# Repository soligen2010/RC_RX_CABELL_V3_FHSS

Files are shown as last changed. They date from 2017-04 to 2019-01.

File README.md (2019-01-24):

# RC_RX_CABELL_V3_FHSS
## Background
RC_RX_CABELL_V3_FHSS is an open source receiver for remote controlled vehicles.  Developed by Dennis Cabell (KE8FZX)
The hardware for this receiver is an Arduino Pro Mini (using a 5V ATMEGA328P at 16 Mhz) and one or two NRF24L01+ modules.  Both are inexpensively available on-line.  Be sure to get the version of a Pro Mini that has pins A4, A5, A6 and A7 broken out.

The transmitter side of this RC protocol is in the Multi-protocol TX Module project at [https://github.com/pascallanger/DIY-Multiprotocol-TX-Module]( https://github.com/pascallanger/DIY-Multiprotocol-TX-Module).

Since there are on-going changes to the main Multi-protocol branch, if you have issues or are using experimental features please test with the solgen2010 fork, which is the latest version tested with the receiver [https://github.com/soligen2010/DIY-Multiprotocol-TX-Module]( https://github.com/soligen2010/DIY-Multiprotocol-TX-Module).

Note: The no-pulses failsafe feature has not yet been merged into pascallanger. Use the soligen2010 fork if you want to use this feature.

## The Protocol
The protocol used is named CABELL_V3 (the third version, but the first version publicly released).  It is a FHSS protocol using the NRF24L01+ 2.4 GHz transceiver.  45 channels are used from 2.403 through 2.447 GHz.  The reason for using 45 channels is to keep operation within the overlap area between the 2.4 GHz ISM band (governed in the USA by FCC part 15) and the HAM portion of the band (governed in the USA by FCC part 97).  This allows part 15 compliant use of the protocol, while allowing licensed amateur radio operators to operate under the less restrictive part 97 rules if desired.

Each transmitter is assigned a random ID (this is handled by the Multi-protocol TX Module) based on this ID one of 362880 possible channel sequences is used for the frequency hopping.  The hopping pattern algorithm ensures that each hop moves at least 9 channels from the previous channel.  One packet is sent every 3 - 4 milliseconds (depending on options chosen), changing channels with each packet. All 45 channels are used equally.

The CABELL_V3 protocol can be configured to send between 4 and 16 RC channels, however this receiver software is currently only capable of outputting up to 8 channels via PWN or PPM.  This is because only 8 channels were conveniently laid out on the Arduino Pro Mini, and more than 8 channels over PPM would be too slow.  SBUS output allows all 16 channels to be used.

I recommend reducing the number of channels as much as possible based on what your model requires.  Fewer channels will use a smaller packet size, which improves transmission reliability (fewer bytes sent means less opportunity for errors).

The protocol also assigns each model a different number so one model setting does not control the wrong model.  The protocol can distinguish up to 255 different models, but be aware that the Multi-Protocol transmitter software only does 16.

## Hardware
A 5V 16Mhz Arduino Pro Mini and one or 2 NRF24L01+ modules are needed for this receiver.  Be sure to get the version of a Pro Mini that has pins A4 and A5 broken out (and A6, A7 too for telemetry analog inputs).  The [hardware folder](https://github.com/soligen2010/RC_RX_CABELL_V3_FHSS/tree/master/hardware) contains a schematic and a PCB layout using a single transceiver module for PWN or PPM output; however, this version of the PCB has not been tested.  I am still using the previous version of the PCB and modifying it to implement the changes included in the new version. If anyone tries this PCB version, please open an issue let me know how it works. 

There is also a schematic for using 2 NRF24L01 modules for diversity.  If anyone designs a board for this, please contribute it.  This schematic also has the signal inverter needed for SBUS.

The PA+LNA versions of the NRF24L01+ module provide more receiver range and reliability than the non PA+LNA versions, However the less expensive modules also work OK if the on-board antenna is replaced with a better antenna, although randomly some units seem to work well and others not so well.  I recommend range testing each module.  These modules are also typically unshielded, but work better when shielded.  Here is an outline of the modifications (TODO: add pictures)

#### Antenna
* For the PA_LNA module that has an SMA Connector, remove the connector. A small butane torch to heat the connector works well.  When the solder melts, it pulls right off 
* Cut the antenna trace.  On the PA+LNA module cut the trace back far enough so that no portion of the trace extends beyond the ground plane on the back of the board.  For the boards with an antenna, cut the trace leading to the antenna shortly after the last surface mount component (a capacitor, I think).
* Scrape or sand away the solder mask over the antenna trace.  On the boards with an antenna you will also need to sand away the area next to the trace for a ground connection.  For the PA+LNA module you can re-use the ground connections that were used for the connector.
* Tin the ground and antenna attachment points with solder
* Strip back the coax and separate the braid, twisting it into a wire that can be soldered to the ground point. Tin this.
* Strip the center conductor back to within 1mm of where the braided part now ends.  Tin this.
* Solder the coax to the board.  Use hot glue to fix the coax to the board as strain relief.
* On the other end of the coax, strip back and remove the braided ground conductor to leave the center wire exposed to form the antenna. Leave the inner wire insulation on.

I am no expert, but based on the best understand I have been able to achieve on the theory, using RG-178 or RG-316 (both have speed factor of 69.5) the calculated theoretical coax lengths to use are:
* For the shielded portion of the coax, ideally make the length a multiple of 42.5 mm.  170mm seems like a good length. 
* The length of the antenna at the end should theoretically be 32.5mm (based on center frequency of 2.425 GHz.  I don’t have the proper equipment to verify these lengths, experiment for what works best for you.  My tests showed 32mm seems to work better than 32.5 for a monopole antenna.

The antennas that come with the PA/LNA modules on EBay are often not very good.  Get a good antenna for your transmitter.  For the transmitter I use a 5dbi antenna constructed as recommend by Andrew McNeil at [https://www.youtube.com/watch?v=bs8hvXGJdhM](https://www.youtube.com/watch?v=bs8hvXGJdhM).  Good RX and TX antennas make a big difference to performance.

#### Shielding
Shielding will require using 2 layers of heat shrink tubing around the whole module.  

* First solder a bare wire onto a ground point on the board.
* Encase as much of the board as possible in heat shrink tubing, leaving the antenna and ground wire sticking out, and don’t cover the pins.
* Use copper tape to wrap the module as much as possible on the heat shrink tubing, while staying away from the edge of the heat shrink. (Aluminum  tape can work too, but you cant solder to it.)
* Bend the ground wire back over the copper tape and solder it to the copper tape.
* Encase as much of the board as possible again in heat shrink tubing.  Don’t cover the pins. Be sure to cover all the ground wire and copper tape shielding.

These shielding steps are based partially  in the article at [http://blog.blackoise.de/2016/02/fixing-your-cheap-nrf24l01-palna-module/](http://blog.blackoise.de/2016/02/fixing-your-cheap-nrf24l01-palna-module/). Using the heat shrink and soldering the copper tape is a more robust implementation of the same concept.

## Receiver Output
The output method is controlled via the option byte in the protocol header.  See the Taranis Setup section for  more details.
* Sum PPM on Arduino pin D2 (the Roll pin). The channel sequence is AETR, more specifically Roll, Pitch, Throttle, Yaw, AUX1, AUX2, AUX3, AUX4.
* Individual PWM channel output on pins D2 through D9 in the sequence Roll, Pitch, Throttle, Yaw, AUX1, AUX2, AUX3, AUX4.
* SBUS (__Experimental__) output on the TX pin through an inverter.  The channel sequence is AETR, more specifically Roll, Pitch, Throttle, Yaw, AUX1, AUX2, AUX3, AUX4, AUX5, AUX6, AUX7, AUX8, AUX9, AUX10, AUX11, AUX12.  SBUS packets are output every 7 milliseconds.

## Receiver Setup
The receiver must be bound to the transmitter. There are several ways for the receiver to enter Bind Mode.  When a receiver is in bind mode the LED will be on.
* A new Arduino will start in bind mode automatically.  Only an Arduino that was flashed for the first time (not previously bound) does this.  Re-flashing the software will retain the old binding unless the EEPROM has been erased.
* Erasing the EEPROM on the Arduino will make it start up in bind mode just like a new Arduino. The Arduino sketch [here]( https://github.com/soligen2010/Reset_EEPROM) will erase the EEPROM.
* Connect the Bind Jumper, or press the Bind button while the receiver powers on.
* The protocol has a Un-bind command (it erases the EEPROM), after which a re-start will cause the receiver to enter bind mode just like a new Arduino. After an Unbind the LED will blink until the receiver is re-started.

Turn on the transmitter and have it send a Bind packet.  The receiver LED changes from always on to a slow blink when the bind is successful.  Re-start the receiver after the bind and take the transmitter out of Bind mode, then test the connection.

## Fail-safe
The receiver fail-safes after 1 second when no packets are received.  If a connection is not restored within 3 seconds then the receiver will disarm.  
* At fail-safe, the throttle is set to minimum, and the other channels are set to the failsafe value.
* After disarm, the throttle will stay at minimum until the receiver is re-armed.  To re-arm the receiver move the throttle to the minimum position.
* If FailsafeNu Pulses is used, then all output signals cease on failsafe (Both PPM and SBUS signals are discontinued)

When a receiver is bound the failsafe values are reset to the default values, which are throttle minimum and all other channels at mid-point.

### Customizing Fail-safe Values
__Do not set fail-safe values while in flight.__  Due to the length of time it takes to write the new fail-safe values to EEPROM, the receiver may go into fail-safe mode while saving the values, causing loss of control of the model.  Before flying a model, always test the fail-safe values after they have been set.

Fail-safe set mode will set the fail-safe values.  This can be done one of two ways:
* A set-Fail-Safe packet can be sent from the transmitter.  The values from the first packet in a series for set-Fail-Safe packets are saved as the new fail-safe values.  The LED is turned on when a set-Fail-Safe packet is received, and stays on as long as set-Fail-Safe packets continue to be received.  The LED is turned off when set-Fail-Safe values stop being received
* After the receiver has initialized, the bind button (or bind jumper) can be held for one to 2 seconds until the LED is turned on.  The values from the first packet received after the LED is turned on will be saved as the new fail-safe values.  The LED will turn off when the button is released (or jumper removed).

When fail-safe set mode is entered, the LED is turned on and stays on until the failsafe set mode is exited.  Only the values from the first packet received in fail-safe set mode are saved (this is to avoid accidentally using up all of the EEPROMs limited number of write operations)

Values for all channels can be set except for the throttle channel.  The fail-safe for throttle is always the minimum throttle.

If the receiver was bound with Failsafe No Pulses, then customizing values does not apply.

## Safety

__Always remove the props when working on a model!__

The receiver has a dis-arm feature to help prevent the motor from unintentionally spinning, however no system is 100%, so take care whenever you power up a model.  __Keep all body parts, clothing, and other objects out of the path of the prop.__

Many ESCs and flight controllers have an arm sequence where the throttle must be set to minimum or some other condition to be met in order to arm.  This receiver also has the following arm/disarm behavior which complements ESC and flight controller arming behavior.

When powered on the __receiver starts out in an armed state__. However, if no signal is detected within 3 seconds the receiver dis-arms.  The receiver also dis-arms if an RC signal is lost for 3 seconds. While dis-armed, only the minimum value will be sent on the throttle channel.  The receiver will re-arm when it receives an RC signal with a minimum value for the throttle channel.  If your model disarms in while in use, move the throttle to its minimum position to re-arm once the RC signal has been re-established.

Powering on the model before the transmitter will cause the receiver to dis-arm in 3 seconds as long as there is no RC signal.  During this power on time there is no output from the receiver until an RC signal is first received from the transmitter, so the ESC or flight controller will not arm if it requires a signal to arm.

Powering the transmitter off before the model will cause the receiver to dis-arm after 3 seconds, forcing the throttle channel to minimum.

There is a 10k pull-up resistor on pin D2 that is essential for safety when using PPM.  This resistor prevents random signals from being output from the receiver while it is initializing.  

### Sending Stick Commands to ESC

__Stay Safe!  Only do this with props removed!__

The reason the receiver initializes in an armed state to to allow an ESC to be configured with stick commands, which may require the initial throttle setting sent to the ESC to be max throttle. If you power on the transmitter before the model, then when the model acquires the signal the values received will be immediately output.  This means that a high throttle will be immediately output.  __Do not do this if your ESC starts in an armed state!__

Please refer to your ESC documentation for details on configuring it with stick commands.

## Diversity
Diversity is achieved by using 2 NRF24L01 modules, which improves link reliability. Try to orient the antennas close to 90 degrees to each other so at least one antenna has a good orientation to the transmitter antenna.  The use of a second NRF24L01 module for diversity is optional.  The code automatically detects if one or 2 modules are connected.  See the "with diversity" schematic in the hardware folder for how to wire the NRF24L01 modules.

Both modules listen for an incoming packet.  If the primary receiver does not get a packet when expected, the secondary receiver is checked for the missed packet.  After each packet, the primary/secondary receivers are swapped, except in the case where only the primary receiver had the packet, in which case this receiver will retain the primary role.  Telemetry packets are transmitted using the same receiver that was used to read the packet.  If both receivers got the incoming packet, then the packet in the secondary receiver is discarded.  The net effect is that the receivers alternate with each packet, except when only one receiver is receiving, in which case that receiver continues to be used for both the primary receiver and telemetry transmit.

## Taranis Setup using Multi-Protocol Module and Open-TX 2.2

With a Multi Protocol module installed in the Taranis, this is how to configure a model to use this protocol.  These instructions for for a Serial connection using OpenTX 2.2.  These instructions assume some familiarity with using OpenTX on the Taranis.

### Initial Setup 
   
* Press Menu to go to Model Selection and Select the model you with to set up.
* Press Page to get the the Model Setup page.
* Scroll down to the Internal RF section and change Mode to OFF.
* Scroll down to the External RF section and change Mode to MULT.
* In the protocol field to the right of MULT, select Custom.
* In the protocol field to the right of Custom, enter 34.  This is the protocol number. 
  * __This number is temporary.  It likely will need to change when the TX half of this protocol is merged into the main Multi-Protocol project.__
* The next number to the right is the sub-protocol.  For initial setup select 0 or 1.  Valid values are:
  * 0 - Normal usage without telemetry
  * 1 - Normal usage with telemetry (please see the section on telemetry)
  * 6 - Set fail-safe values (see below and the Fail-safe section)
  * 7 - Unbind receiver (see below)
* Receiver No. should be filled in with the model number.
* Move down to the Option value.  This value must be calculated to configure the protocol.  This is done by entering a number that is the sum of the options you wish to use.  Select the values from below and add them together to get the option value.
  * _Channel Reduction_ reduces the number of channels transmitted.  This also reduces the size of the packet, which improves reliability. (Fewer bytes sent equates to less opportunity for error.)  For best reliability reduce the number of channels to the minimum number needed for the model. Note that at least 4 channels must always be sent.  Choose one of the following to add into the Option value:
    * 0  - Send 16 channels
    * 1  - Send 15 channels
    * 2  - Send 14 channels
    * 3  - Send 13 channels
    * 4  - Send 12 channels
    * 5  - Send 11 channels
    * 6  - Send 10 channels
    * 7  - Send 9 channels
    * 8  - Send 8 channels
    * 9  - Send 7 channels
    * 10 - Send 6 channels
    * 11 - Send 5 channels
    * 12 - Send 4 channels
  * _Output Mode_ indicates how the receiver should output the channels.  Choose one of the following to add into the Option value:
    * 0  - Output servo PWM signals on pins D2 through D9 for channels 1 to 8
	* 16 - Output channels 1 to 8 using PPM on pin D2
	* 32 - Output channels 1 to 16 using SBUS __(Experimental)__
  * _Transmitter Power_ Overrides the Multi-Protocol's normal high power setting.  See comments on power setting below.  Choose one of the following to add into the Option value:
    * 0 - Use the NRF24L01+ HIGH power setting.  This is the normal Multi-Protocol module behavior.
    * 64 - Use the NRF24L01+ MAX power setting instead of the HIGH power setting.  This over-rides the normal Multi-Protocol module behavior.
  #### Notes on Power Setting
  Using an NRF24L01+ with PA/LNA outputs 25 milliwatts for HIGH power and 100 milliwatts for MAX power.  Despite this there are reports that using MAX power on inexpensive Chinese modules provides worse range than using the HIGH power setting due to the noise added by the extra amplification and the lower quality Chinese components.  By adding shielding and using a good antenna, I get better range using MAX power even with Chinese components.  Your results may vary so range test your equipment and use the setting that provides the best results.

### Binding Receiver
* Turn on the receiver in Bind Mode. (See receiver setup above.)
* In the transmitter Navigate to the Model Setup page.
* In the External RF section, highlight BIND and press enter.
* The receiver LED will blink when the bind is successful.
* Restart the receiver.
 
### Unbinding Receiver

In order to un-bind a receiver using the transmitter, a model bound to the receiver must be configured in the transmitter.  With a model selected that is bound to the receiver:
* Navigate to the Model Setup page.
* Go to the External RF section.
* Change the sub-protocol (second number after "Custom") to 7.
* The receiver LED will fast blink when the un-bind is successful.
When the receiver is restarted, it will start in Bind mode.

### Setting Failsafe Values

__Do not set fail-safe values while in flight.__ Please see the Customizing Fail-safe Values section for more information.

* Navigate to the Model Setup page.
* Go to the External RF section.
* Place all switches in the desired fail-safe state.
* Move the sticks to the desired fail-safe state.  Hold them in this position until the fail-safe settings are recorded by the receiver.
* While holding the sticks, change the sub-protocol (second number after "Custom") to 6.  DO not go past 6.  If you even briefly go to 7 the receiver will un-bind.
* When the LED is turned on, the Fail-safe settings are recorded
* Change the sub-protocol back to its original setting. The LED will turn off.

Always test the Fail-safe settings before flying.  Turning off the transmitter should initiate a Fail-safe after one second.

### Setting Failsafe No Pulses (Experimental)

Failsafe No Pulses can only be set at bind time.  All servos will receive no pulses during a fail-safe, so custom fail safe values do not apply.  If the receiver is on SBUS output mode, the SBUS output is stopped during failsafe.

* Unbind the receiver.
* Navigate to the Model Setup page.
* Go to the External RF section.
* Change the sub-protocol to 5.  
* Perform the Bind procedure.
* Change the sub-protocol to the desired setting for flying.

If your output goes to a flight controller via SBUS, and the flight controller honors the SBUS failsafe flag (which is typical), then you probably do not want to use No Pulses because the SBUS protocol handles the failsafe appropriately.

Always test the Fail-safe settings before flying.  Turning off the transmitter should initiate a Fail-safe after one second.

## Telemetry

When the sub-protocol is set to Normal with Telemetry, the receiver sends telemetry packets back to the transmitter.  Three values are returned, a simulated RSSI, and the voltages on the Arduino pins A6 and A7.  A receiver module with diversity is recommended when using telemetry to increase the reliability of the telemetry packets being received by the transmitter.

### RSSI

Because the NRF24L01 does not have an RSSI feature, the RSSI value is simulated based on the packet rate.  The base of the RSSI calculation is the packet success rate from 0 to 100.  This value is re-calculated approximately every 1/2 second (every 152 expected packets).  This success percentage is then modified in real time based on packets being missed, so that if multiple packets in a row are missed the RSSI value drops without having to wait for the next re-calculation of the packet rate.

In practice, the packet rate seems to stay high for a long range, then drop off quickly as the receiver moves out of range.  Typically, the telemetry lost warning happens before the RSSI low warning.

The RSSI class encapsulates the RSSI calculations. If you are so inclined, feel free play with the calculation. If anyone finds an algorithm that works better, please contribute it. 

### Analog Values

Analog values are read on Arduino pins A6 and A7.  Running on a, Arduino with VCC of 5V, only values up to 5V can be read.  __A value on A6 or A7 that exceeds the Arduino VCC will cause  damage__, so care must be taken to ensure the voltage is in a safe range.

Values from pins A6 and A7 come into a Taranis transmitter as telemetry values A1 and A2.  You can use either of these to read battery voltage or the output of current sensor.  The following article explains how to input battery voltage to A2 on an Frsky receiver using a voltage divider.  The same method can be used to read battery voltage on this receiver.  [http://olex.biz/tips/lipo-voltage-monitoring-with-frsky-d-receivers-without-sensors](http://olex.biz/tips/lipo-voltage-monitoring-with-frsky-d-receivers-without-sensors).

The values sent are 0 - 255 corresponding to 0V - 5V.  This will need to be re-scaled to the actual voltage (or current, etc.) in the transmitter on the telemetry  configuration screen.

## Flashing Firmware

The Arduino development environment is required to compile the code and write the firmware to the Arduino Pro Mini. If you are not familiar with this, here are some resources to help you.

* [https://www.arduino.cc/en/Guide/HomePage](https://www.arduino.cc/en/Guide/HomePage)
* [https://www.arduino.cc/en/Guide/ArduinoProMini](https://www.arduino.cc/en/Guide/ArduinoProMini)
* [https://www.youtube.com/watch?v=78HCgaYsA70](https://www.youtube.com/watch?v=78HCgaYsA70)
* [http://lab.dejaworks.com/programming-arduino-mini-pro-with-ftdi-usb-to-ttl-serial-converter/](http://lab.dejaworks.com/programming-arduino-mini-pro-with-ftdi-usb-to-ttl-serial-converter/)

## Receiver Test Harness

The receiver code can be compiled as a test harness.  What this means is that instead of outputting the normal output signals, statistics are displayed on a 16x2 LCD screen about the packet success rate. To enable Test Harness mode, uncomment the following line in TestHarness.h.  No output will go to servos, flight controller, etc. when in test harness mode.

```//#define TEST_HARNESS```

The LCD displays 5 numbers.
* Line 1:  Packet success rate (percent); Number of missed packets in a row; The number of time the secondary receiver  recovers a packet the primary receiver  missed
* Line 2:  The number of good packets received; The number of missed or bad packets

The LCD pin connections are:

  LCD D4_PIN = Arduino D9
  LCD D5_PIN = Arduino D8
  LCD D6_PIN = Arduino D7
  LCD D7_PIN = Arduino D6
  LCD RS_PIN = Arduino D5
  LCD EN_PIN = Arduino D4
  
More information on connecting the LCD is at [https://www.arduino.cc/en/Tutorial/LiquidCrystalDisplay](https://www.arduino.cc/en/Tutorial/LiquidCrystalDisplay).  However, I suggest using a 330 or 470 ohm resistor instead of the 220 ohms listed in the article to avoid pulling over 20 mA from the Arduino pin connected to the LED back-light.

You can also connect an I2C LCD display.  This may require additional code editing and the installation of a different LCD library (from [https://bitbucket.org/fmalpartida/new-liquidcrystal/downloads/](https://bitbucket.org/fmalpartida/new-liquidcrystal/downloads/)).  Please see the comments in TestHarness.h for more details.

## Packet Format

```
typedef struct {
   enum RxMode_t : uint8_t {   
         normal                 = 0, 
         bind                   = 1,
         setFailSafe            = 2,
         normalWithTelemetry    = 3,  
         telemetryResponse      = 4,
         bindFalesafeNoPulse    = 5,   (experimental)
         unBind                 = 127
   } RxMode;
   uint8_t  reserved = 0; /* Contains the channel number that the packet was sent on in bits 0-5 
                          */
   uint8_t  option;
                          /*   mask 0x0F    : Channel reduction.  The number of channels to not send (subtracted from the 16 max channels) at least 4 channels are always sent.
                           *   mask 0x30>>4 : Receiver output mode
                           *                  0 (00) = Single PPM on individual pins for each channel 
                           *                  1 (01) = SUM PPM on channel 1 pin
                           *                  2 (10) = SBUS output
                           *                  3 (11) = Unused
                           *   mask 0x40>>6   Contains max power override flag for Multiprotocol TX module. Also sent to RX
                           *                  The RX uses MAX power when 1, HIGH power when 0
                           *   mask 0x80>>7   Unused 
                           */  
   uint8_t  modelNum;
   uint8_t  checkSum_LSB;   // Checksum least significant byte
   uint8_t  checkSum_MSB;   // Checksum most significant byte
   uint8_t  payloadValue [24] = {0}; //12 bits per channel value, unsigned
} CABELL_RxTxPacket_t;   
```
Each 12 bits in payloadValue is the value of one channel.  The channel order is EART (i.e. Pitch, Roll, Yaw, Throttle, AUX1, AUX2, AUX3, AUX4).  Valid values are in the range 1000 to 2000.  The values are stored big endian.

Using channel reduction reduces the number of bytes sent, thereby trimming off the end of the payloadValue array.

## Credits
davidbuzz on github.  Although none of his code is in this project, my very first foray into DIY rx/tx was based on his esp8266_wifi_tx project.

iforce2d on YouTube.  Although none of his code is in this project, the work he did with the NRF24L01 was a big inspiration.

All the contributors to the pascallanger/DIY-Multiprotocol-TX-Module project on GitHub.  This is a great contribution to the RC community and houses the TX side of this protocol.  

All the contributors to the nRF24/RF24 project on GitHub.  This library was essential to learning to use the NRF24L01.

All the contributors to Arduino Core and standard libraries.  Especially the Servo library, which I modified to adapt to the needs of this project.

The author of the PPM algorithm at https://code.google.com/archive/p/generate-ppm-signal/ I believe this to be david.hasko94@gmail.com

The channel sequence is generated using a permutation algorithm described at http://stackoverflow.com/questions/7918806/finding-n-th-permutation-without-computing-others 

Nick Gammon for his tutorials on interrupts and async reading of ADC pins at https://www.gammon.com.au/adc

My wife, for tolerating the obsession I have had with this project.

## License Info
Copyright 2017 - 2019 by Dennis Cabell (KE8FZX)
 
To use this software, you must adhere to the license terms described below, and assume all responsibility for the use of the software.  The user is responsible for all consequences or damage that may result from using this software. The user is responsible for ensuring that the hardware used to run this software complies with local regulations and that any radio signal generated from use of this software is legal for that user to generate.  The author(s) of this software assume no liability whatsoever.  The author(s) of this software is not responsible for legal or civil consequences of using this software, including, but not limited to, any damages cause by lost control of a vehicle using this software.   If this software is copied or modified, this disclaimer must accompany all copies.
 
This project is free software: you can redistribute it and/or modify it under the terms of the GNU General Public License as published by the Free Software Foundation, either version 3 of the License, or (at your option) any later version.

RC_RX_CABELL_V3_FHSS is distributed in the hope that it will be useful, but WITHOUT ANY WARRANTY; without even the implied warranty of MERCHANTABILITY or FITNESS FOR A PARTICULAR PURPOSE.  See the GNU General Public License for more details.

You should have received a copy of the GNU General Public License along with RC_RX_CABELL_V3_FHSS.  If not, see <http://www.gnu.org/licenses/>.

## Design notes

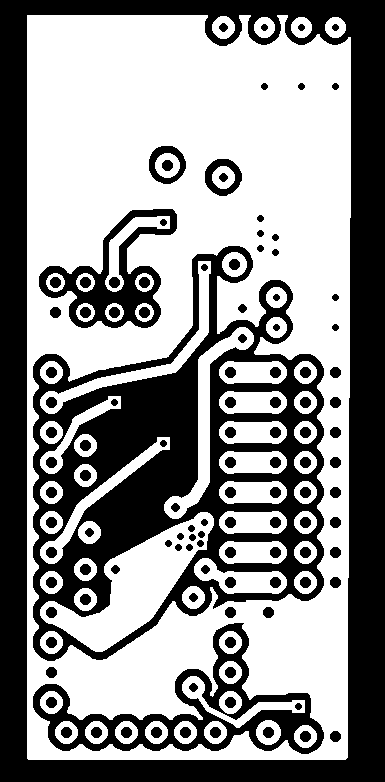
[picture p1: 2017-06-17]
hardware/BoardLayoutNoDiversityNoSBUS_bottom_300dpi.png

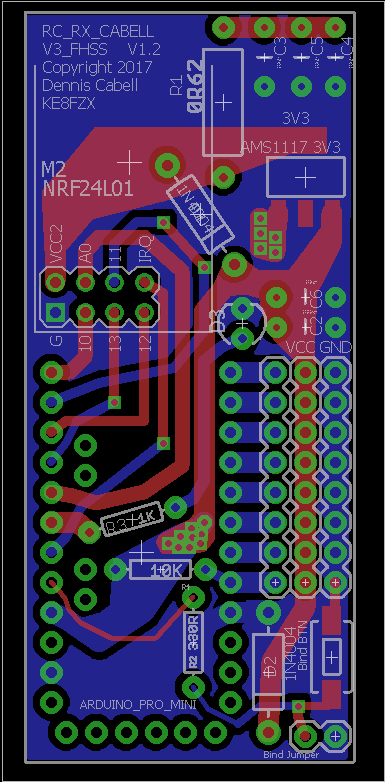
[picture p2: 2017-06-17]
hardware/BoardLayoutNoDiversityNoSbus.png

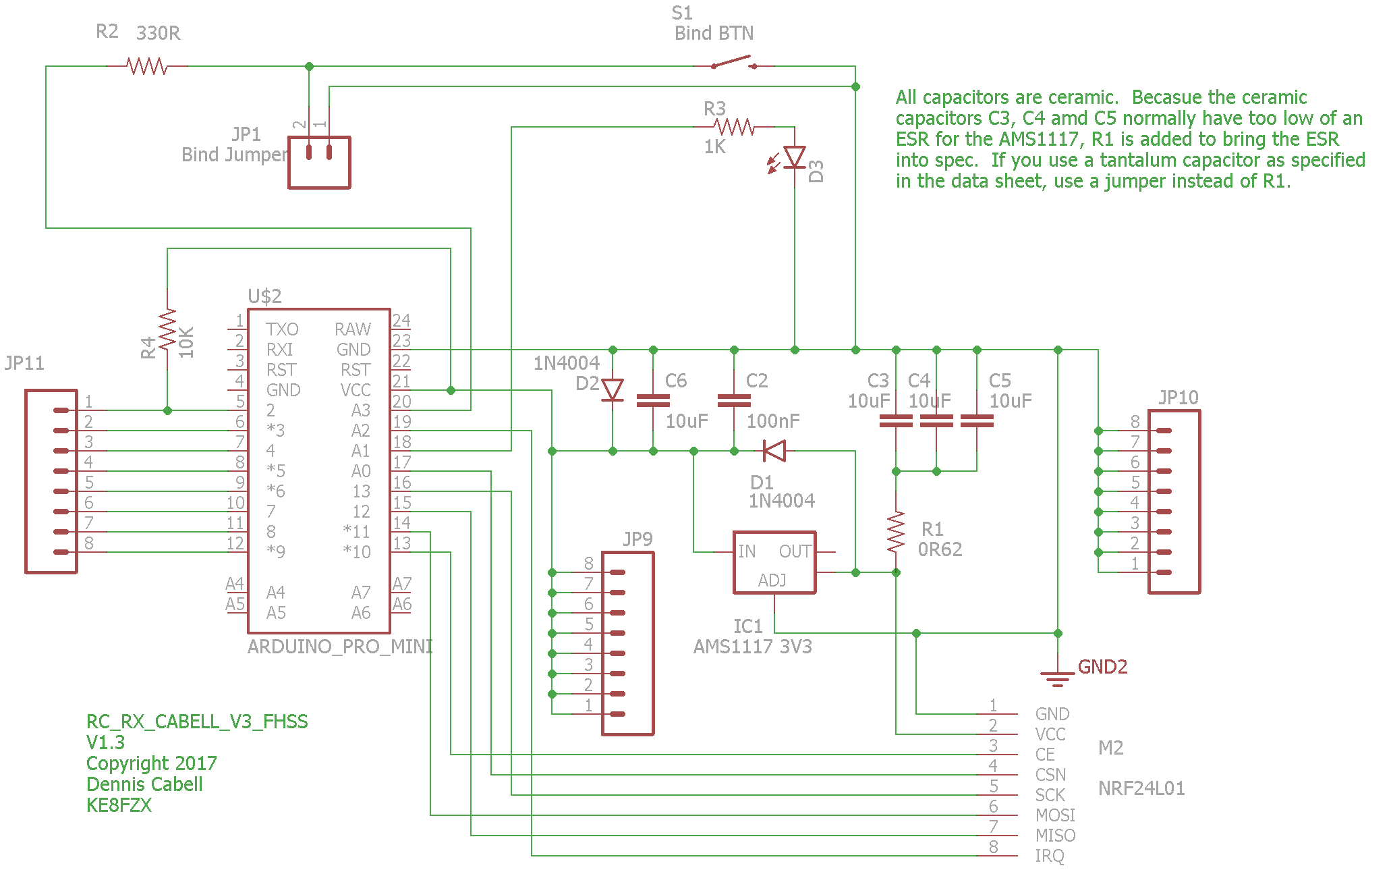
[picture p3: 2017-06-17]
hardware/SchematicNoDiversityNoSBUS.png

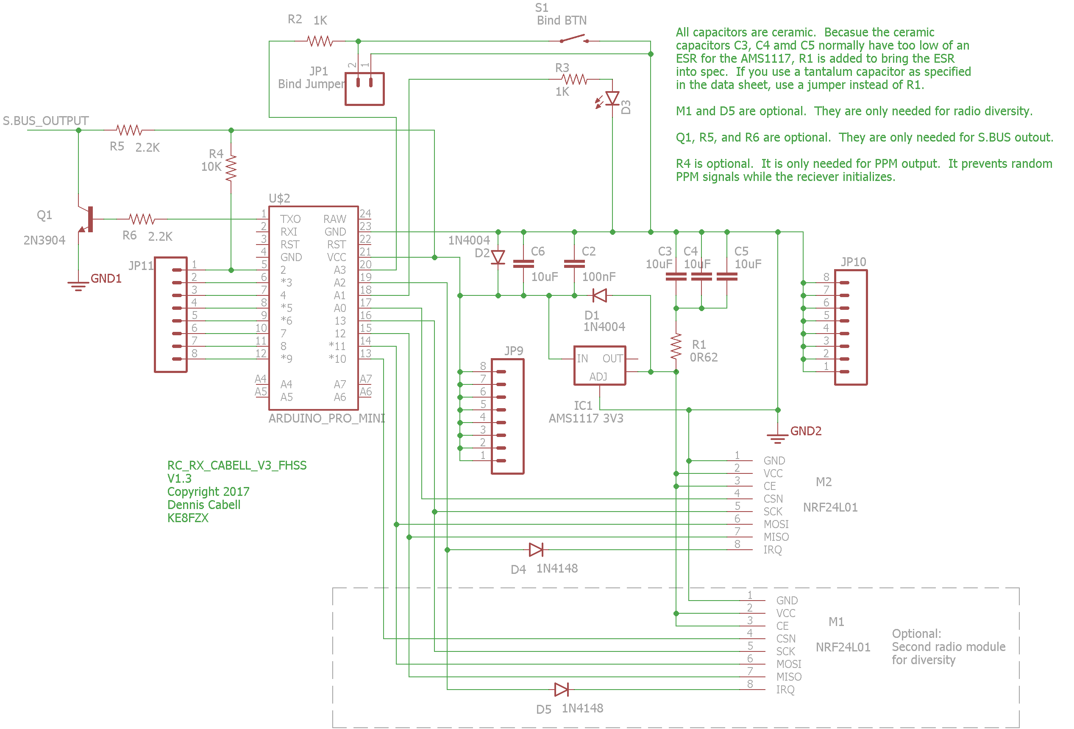
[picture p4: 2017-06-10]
hardware/SchematicWithDiversityWithSBUS.png

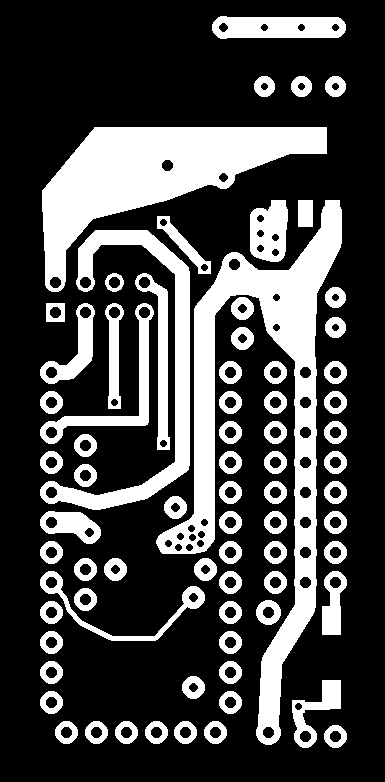
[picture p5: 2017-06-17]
hardware/BoardLayoutNoDiversityNoSbus_top_300dpi.png

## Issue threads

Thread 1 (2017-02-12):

Where is the code

tipouic, 2017-02-12:
Can you push one old version in order to see the evolution ?
Thank you

soligen2010, 2017-02-12:
Thanks for the interest.  Unfortunately this project has slowed.  Due to a back injury I have had trouble sitting at my desk for any length of time.

The good new is that yesterday I flew 3 models using this protocol, (but not using Multiprotocol as the TX). and today I updated my board layout.

My plan is to:

Update my Multiprotocol code fork and test it.
Write some documentation.
Upload everything.

Hopefully all this week.

After that, I want to work on antenna design then do range/reliability testing.

soligen2010, 2017-03-11:
The first release of the code has been uploaded.  Enjoy :)

Closed 2017-03-11.

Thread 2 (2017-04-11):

Compiling error with Arduino IDE 1.68

Gabapentin, 2017-04-11:
Hi Dennis,
sorry for annoyance
I have tried to compile the sketch on a fresh Arduino IDE 1.68 installation
but the compiler give me some errors:

-----------------------------------------------------------------------------------------------------------
Arduino:1.6.8 (Windows 7), Scheda:"Arduino Pro or Pro Mini, ATmega328 (5V, 16 MHz)"

sketch\MyServo.cpp: In function 'void MyServoInterruptOneProcessing()':

sketch\MyServo.cpp:85:43: warning: 'void MyServoInterruptOneProcessing()' was declared 'extern' and later 'static' [-fpermissive]

 static void MyServoInterruptOneProcessing()

    ^

In file included from sketch\MyServo.cpp:30:0:

sketch\MyServo.h:125:6: note: previous declaration of 'void MyServoInterruptOneProcessing()'

 void MyServoInterruptOneProcessing();

                 ^

sketch\MyServo.cpp: At global scope:

sketch\MyServo.cpp:189:39: warning: unused parameter 'timer' [-Wunused-parameter]

 static void finISR(timer16_Sequence_t timer)

                                                                 ^

sketch\RX.cpp:35:26: fatal error: ClickEncoder.h: No such file or directory

 #include <ClickEncoder.h>

                        ^

compilation terminated.

Thanks a lot in advance for your reply

BR's Pat

soligen2010, 2017-04-13:
Sorry for the delay getting back to you.  I have been down with the flu.

I use Arduino 1.8.0 and it compiles.  Can you please try removing static from

static void MyServoInterruptOneProcessing()

and see if they solves it on 1.6.8.

Thanks

Gabapentin, 2017-04-13:
Thanks a lot Dennis

don't worry I'm not in a hurry

In the meantime I've removed static and installed missing "encoder" library

now seems to be working

get well soon!

BR's Pat

soligen2010, 2017-04-13:
I am glad that worked.  I made the change and also added the encoder library to the comments as a dependency.

As this appears resolved, I am closing this issue.

soligen2010, 2017-05-22:
FYI, in an effort to lighten up the code a bit, the encoder library is not linger needed

Closed 2017-04-13.

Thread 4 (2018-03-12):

Feature request: No pulse failsafe option

qubic, 2018-03-12:
It is more convenient to setup failfafe in flight controller, no pulse failsafe is a good choice in this scene

soligen2010, 2018-03-14:
Thanks for your suggestion.

Can you provide more details on how this would need to be implemented?  Are we talking about the SBUS output or the servo outputs?

SBUS has a fail-safe flag in the packet, and the receiver sets this flag appropriately on SBUS output when there is a failsafe.  Iis this what no-pulses is supposed to do? Do you know if flight controllers honor this flag?

qubic, 2018-03-15:
Just stop sending signals to the flight controller in ppm mode;
Cleanflight and Betaflight honor the sbus fail-safe flag, the cleanflight community has implemented it, https://github.com/cleanflight/cleanflight/issues/2549

soligen2010, 2019-01-21:
I just uploaded a new version with no-pulses capability.  It seems to work but has very limited testing at this point.  Please test if you can.  You will need to use my fork of Multi-protocol with the latest RX code as I have not merged my MultiProtocol changes back yet.  In this mode both PPM signals and SBUS signals are stopped on failsafe.

qubic, 2019-01-30:
OK, i will test it later.

qubic, 2019-06-30:
I have tested the latest firmware, the no-pulse works as expected.

By the way is the D4 ( SchematicWithDiversityWithSBUS.png ) optional if only one module is connected ?

soligen2010, 2019-07-25:
Thanks for testing it.

Yes, D4 is not needed if only one NRF24L01 is connected

soligen2010, 2020-06-16:
Closing as this feature is complete

Closed 2020-06-16.

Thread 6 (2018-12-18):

Compilation error

pierrotm777, 2018-12-18:
Hello,
I try to compile your project with the 1.8.8 ide but i obtain an error .
C:\Users\pierre\AppData\Local\Temp\arduino_build_756723\sketch\RX.cpp: In function 'setFailSafeValues':

C:\Users\pierre\AppData\Local\Temp\arduino_build_756723\sketch\RX.cpp:650:1: internal compiler error: Segmentation fault

 }

 ^

Please submit a full bug report,

with preprocessed source if appropriate.

See <http://gcc.gnu.org/bugs.html> for instructions.

lto-wrapper.exe: fatal error: C:\tmp\Arduino_Compilateur\arduino-1.8.5\hardware\tools\avr/bin/avr-gcc returned 1 exit status

compilation terminated.

c:/tmp/arduino_compilateur/arduino-1.8.5/hardware/tools/avr/bin/../lib/gcc/avr/5.4.0/../../../../avr/bin/ld.exe: error: lto-wrapper failed

collect2.exe: error: ld returned 1 exit status

Utilisation de la bibliothèque SPI version 1.0 dans le dossier: C:\tmp\Arduino_Compilateur\arduino-1.8.5\hardware\arduino\avr\libraries\SPI
Utilisation de la bibliothèque EEPROM version 2.0 dans le dossier: C:\tmp\Arduino_Compilateur\arduino-1.8.5\hardware\arduino\avr\libraries\EEPROM
exit status 1
Erreur de compilation pour la carte Arduino Pro or Pro Mini

Can you help me please ?

Thanks

soligen2010, 2018-12-18:
I upgraded to 1.8.8 and it compile fine for me, so it must be something wrong with your installation or settings.

All I could suggest is to make sure you have the right board selected - I use the Arduino Nano board selection. It seems to work fine for the Pro Mini boards.

krukhlis, 2018-12-18:
There was a buggy version of Arduino recently released, tons of people have suffered from lto-wrapper error. Could be the same. In the most recent version they say they have fixed it:
http://forum.arduino.cc/index.php?topic=576749.0

per1234, 2018-12-19:
@krukhlis I think that is a different issue. This is the correct one:
https://github.com/arduino/Arduino/issues/7949

This bug is difficult to reproduce. It comes and goes for no apparent reason. I've also only seen it occur for people using Windows. So it's not surprising that it did not occur for @soligen2010.

I don't think the issue is caused in any way by the code in this library and I don't think any changes to this code could fix it (though they might make it disappear purely by chance).

There is a beta release of a new AVR toolchain that is intended to fix the bug. If you want to give it a try, you can install it by doing this:

1. File > Preferences
2. In the "Additional Boards Manager URLs" field, add http://downloads.arduino.cc/packages/package_avr_7.3.0_index.json
3. Click "OK".
4. Tools > Board > Boards Manager
5. Wait for downloads to finish.
6. Click on "Arduino AVR Boards".
7. Click "Update".
8. Wait for the update to finish.
9. Click "Close".
10. Try compiling again.

pierrotm777, 2018-12-19:
Thanks for your answer. I shall try to update my board definition.

Le mar. 18 déc. 2018 à 23:07, krukhlis <notifications@github.com> a écrit :

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

pierrotm777, 2018-12-19:
I have tried to build a prototype based on a nrf24l01 without pa lna. I use
for my test a uno board with a converter level for moso, miso, sck ans csn.
Ce is connected to 3,3v. Irq with a 1n4148.
I use a Pascallanger multiprotocol module that running already with a
cc2500 (frsky d, x ans Corona protocols) and A7105 (flysky 2A protocol).
I use a a1117 for the 3,3v and 10uf /100nf capacitors.
I have a Led on A1 et simulate strap bind with à 4,7k between A3 ans gnd.
When i start my uno, the Led stay on, with or without strap.
On tx, i have define a custom (34,0) mode.
If i launch a bind, the receiver's led stay on.
Do you think that my issue is my uno board (no A6 and A7)?

I use this schematic but without 1n4007 diode and without resistor on d2
pin.

Thanks for your help.

Pierre

Le mer. 19 déc. 2018 à 08:29, pierrotm777 <pierrotm777@gmail.com> a écrit :

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

soligen2010, 2018-12-19:
If it has never been bound it will always boot into bind mode even regardless of the state of A3.  Did you get it to successfully bind?  The LED should bling when the bind is complete.  If it never blinked, then there is no bind and it just keeps re-booting into bind mode,

pierrotm777, 2018-12-19:
I see that the schematic that use only one nrf24l01 has the ce pin
connected to d10 and not to 3,3v. Do you think that i  must to connect d10
pin to ce ?

Le mer. 19 déc. 2018 à 13:19, Dennis <notifications@github.com> a écrit :

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

soligen2010, 2018-12-19:
No, I don't think it is any of those things you suggested.  I think you maybe never bound the receiver. Did you get the successful bind indicated by the blinking LED or not?

pierrotm777, 2018-12-19:
No bind and no blink for now.

Le mer. 19 déc. 2018 à 22:03, Dennis <notifications@github.com> a écrit :

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

pierrotm777, 2018-12-21:
Hello,
I have tested the New board definition and now I can compile without error.
But i can't bind my radio with the receiver. The serial Windows return well
that sync is waiting, but the Led stay always on.
Just one question.
I use my uno board with several project and my EEprom isn't empty. Do you
think I need to clear it before ?

Le mer. 19 déc. 2018 à 13:19, Dennis <notifications@github.com> a écrit :

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

pierrotm777, 2018-12-21:
Other little question, can you explain me what is the utility of d1 and d2
(1n4004)?
It's important or I can not use them ?

Le ven. 21 déc. 2018 à 09:59, pierrotm777 <pierrotm777@gmail.com> a écrit :

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

soligen2010, 2018-12-21:
Hear are things to do next.

In the first few lines of the serial output it displays if the primary and/or secondary radio is detected. What do these lines indicate?

If the primary radio is detected, and if you used a diode in the IRQ it is oriented correctly (the diode is only needed for 2 radios), the the fault is probably in the TX side.  Share more details on the TX module.  What hardware, what compile options.  You have to be sure this protocol is compiled in.  I have only tested with my fork of the multi-protocol code, so you could try to use the fork under soligen2010.  I dont know if the protocol works on the 32bit versions (like the iRange) as I don't have one to test with.

If you have just one radio with CSN on D14 (aka A0), the the CE pin can be tied to either D10 or +3.3,  it should not make a difference, but feel free to try both if you like.

EEPROM does not need to be erased.  The LED on indicates bind mode, so your old EEPROM data will be over-written when bind is successful.  If LED doesn't turn on, then erasing EEPROM is a way to get into bind mode without needing a button.

D1 & D2 are flyback diodes to protect against possible reverse voltage spikes.  Inductors (motors/servos) can generate these spikes.  If you have no servos or motors connected, they are optional.

Also, you can try removing the level shifters.  The NRF24L01 is 5V tolerant so they are not needed.  If the shifters are not bi-directional, then they would not work.

pierrotm777, 2018-12-21:
I use this module on my transmitter, but a I have also tested another
nrf24l01 without pa lna in the transmitter.
€ 3,80  16� réduction | E01-ML01DP5 Longue Portée SPI nRF24L01P 2.4 ghz 100
mw SMA Antenne IoT Sans Fil Émetteur-Récepteur Émetteur Récepteur nRF24L01P
RF Module
https://s.click.aliexpress.com/e/bDCRjd8l

Le ven. 21 déc. 2018 à 19:17, Dennis <notifications@github.com> a écrit :

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

soligen2010, 2019-01-21:
It has been a month and no new information as been posted on the recommended next steps for this, so closing the issue.  Re-open it if you get more details to share.

pierrotm777, 2019-01-22:
Sorry,
I wait a new nrf24l01 with pa lna feature for a new test.
I have done my test with an Uno board and not a pro mini. So I and I don't know if use an Uno with your code is a good idea

soligen2010, 2019-01-22:
Neither of those things should make a difference

Closed 2019-01-21.

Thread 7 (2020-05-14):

Can you please advise me PWM MOTOR DRIVER

stanekTM, 2020-05-14:
Hi Soligen,
Can you please advise me.
I need to change channels AUX_1-AUX_4.
I need the PWM outputs of the motor control to go from these outputs, depending on the position of the control levers.
I'm completely lost in your code.
So far I have a functional simple communication with the control, but I need to keep your protocol in MULTI.
I will be happy for any suggestions and advice.
Thank you for this beautiful project.

George
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

soligen2010, 2020-06-09:
Mapping to channels is something you would do in the transmitter, not in the RX code. All the RX outputs are PWM, so you need to map the sticks to the desired channels in the transmitter.  You should be able to find tutorials on-line for your transmitter than can explain this much better than I can.

My other suggestion would be just to wire the things differently on the receiver so the channels with the data you want are wired to the correct port of your PWM controller.

I do highly recommend that **you not change the Throttle channel**.  For safety, this channel has a disarm feature when the signal is lost.

stanekTM, 2020-06-09:
Thanks to Soligen for the suggestions
work in progress, this protocol will be transferred to the "OpenAVRc" project, for direct control of SPI thanks to our developer.
You could add some information to your TX "Cabell" transmitter, such as a diagram, photo, etc. The TX transmitter looks interesting and you don't always need a big processor.
Thank you George

soligen2010, 2020-06-16:
For me, the transmitter project is obsolete.  I transferred the protocol to the MultiProtocol project and that is what I use.  Making changes for each model was just too painful in the TX project because code needed to be re-compiled for each change.  With MultiProtocol, all the model editing is done with OpenTX (or other TX software), and is what I recommend.

I have no plans to re-visit or add documentation for the TX project - I only uploaded it to Github in case someone wanted it and was willing to wade through the code to figure it out.  The code organization is not the greatest - it grew organically as I learned what I wanted to do with the protocol.  This is why I turned off the ability to open issues on the TX project.  I think the RX code is better organized.

stanekTM, 2020-06-16:
Hi Denis,
Yes, I understand, I mainly use the OpenAVRc and OpenTX pistols.
I built my own "RF laps counter" for RC car races. I'm currently working on micro cars, so I was mainly interested in your great RX with the integration of motor drivers. For friends, I want to build a simple basic Cabell TX 2x joystick from the TX set transmitters, no display. I'll see how I manage integration on the ATmega 328P. Making pistol transmitters based on OpenTX or MULTI would drive me crazy.
Thank you for the information and protocol.
Regards George

Closed 2020-07-08.

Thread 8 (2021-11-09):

RSSI does not recover when conditions improve

philj404, 2021-11-09:
Hello, and thank you for providing this useful library.  I have used it to connect a (commercial) Jumper T12 transmitter to my custom tracked-robot controller.

But... I have run into a few issues along the way.  When I configure to use telemetry the transmitter reports signal quality gets worse and worse, and never really recovers -- the reported RSSI tends to sink to zero.  But when I instrument the code, it appears the receiver usually recovers packets 94%-98% of the time.

I'm still investigating why the receiver is failing to recover so many packets, but I don't think RSSI should go to zero for a 90% or better packet success rate.  (I really want a 100% success rate, but for now I will settle for an RSSI indicator which can detect minor improvements.)

I think the ```sequentialMissTrack``` value can penalize packet failures quite severely.  I understand that it might be necessary, but the penalty for a short sequence of bad packets can stretch out to a rather long recovery time.

I made a change (https://github.com/philj404/RC_RX_CABELL_V3_FHSS/tree/improveTelemetry) which resets the ```sequentialMissTrack``` packet quality value after using it to calculate RSSI, and sending it to the transmitter.  This avoids penalizing later readings with previously-logged packet misses.

If you think it might be helpful, I can set up a pull request for you to consider.

soligen2010, 2021-11-10:
Telemetry never worked well, and I never run with telemetry anymore because I got tired of all the RSSI warnings. If I have a bug in there causing the issues and you have a fix, or even if you come up with a whole other algorithm that works well, I would like to see it.

Just a note: The RSSI is a simulation and not true RSSI because the NRF24L01 doesn't report a useful signal strength, so I would never expect it to be as good as a protocol based on a chip that has RSSI in hardware (like FRSky's protocol)

philj404, 2021-11-10:
Yes, it looks like the returned value is closer to "received packet success rate in percent" rather than some more technically correct value in dB.  I'm OK with that because it is easier to calculate and understand.

I will set up a pull request with my changes.  If you would like to merge these changes (and they work), please do so.  If there is some reason they will not work, go ahead and reject the change.

I like having some NRF24L01 example code which works with an off-the-shelf transmitter!  That lets me focus on getting the robot working.

philj404, 2021-11-10:
See #10.

soligen2010, 2021-11-12:
I refreshed my memory on my code and I understand your PR, but I think there is a better way to achieve it.  The getRSSI method gets called every packet, so by resetting the sequential count, it basically completely disables the sequential count penalty/recovery feature..

A better way to do this is this is by adjusting these values in RSSI.h

```
#define RSSI_MISS_ADJUSTMENT            5                     // Each consecutive miss deducts this from the packet rate
#define RSSI_MISS_ADJUSTMENT_RECOVERY   1                     // The rate at which a hit removes the miss adjustment
```
You can achieve the same thing by setting RSSI_MISS_ADJUSTMENT to zero.  Using these you can tune the behavior.  for example Instead of turning it off you can set the adjustment small and recovery high (opposite of what I have), or anything in between, or turn it off.

Based on this I am going to decline your PR.  I hope you take this suggestion and play with the numbers instead of the change you made.  I'd be interested in what numbers you end up liking.

And on another note, you shouldn't need to comment out the code for the second NRF24L01.  The code automatically determines if there is one or 2 connected.  However, packet rates are much better with 2.  Orient the antennas at 90 degrees to each other.

philj404, 2021-11-12:
Thank you for reviewing the change, and clarifying how to better customize settings for this receiver.  I will make local changes and report back if I discover anything.

I MAY add a second receiver for diversity, but I didn't anticipate it when I originally wired my shield. I will have to figure out how to fit it in.

Originally I was using the TMRh/RF24 library, without any frequency hopping.  Its reliability was more consistent, but I need a protocol compatible with this transmitter. I think the base transmitter/receiver communication is OK.  I suspect something is going on with frequency synchronization.  If I discover something useful I will let you know.

In the meantime 94% to 100% packet success rate is still quite good.  I never saw two failures in a row, so any failure only added ~4ms of latency. It is still way faster than many protocols, and overkill for my robot.

soligen2010, 2021-11-13:
That is the base library I use too ( a slightly tweaked version), but there are other modes this chip can run in if you use that library that may seem to help reliability.  You can have the feature to ACK and auto-resend missed packets.  I don't use this feature because if a packet is missed, there is no point in re-sending the missed packet, because the next packet will be more up-to-date anyway.

philj404, 2021-11-14:
I was using the RF24 "receiver sends ACK with a payload" feature before I found your code.  It works, but I found I had to prepare the payload in advance, and once prepared it was not easily updated -- you had to wait until a new packet was received and the ACK was transmitted.  So intermittent connections could end up with very stale updates.

Your code is more responsive with recent RSSI/voltage updates (with more work for switching the hardware from "receive" to "transmit" and back).  Timing calculations get _much_ easier if you avoid retries if a handshake is missed, and only send one fixed-size packet before changing channels.

I guess if you are hopping frequencies, switching between "transmit" and "receive" all the time isn't that much extra effort.

Closed 2021-11-14.

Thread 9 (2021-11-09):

inconsistent use of micros()/millis() in getPacket()?

philj404, 2021-11-09:
While trying to figure out how to get up to 100% received packet reliability, I came across something that confused me:
In RX.cpp getPacket(), ```lastRadioPacketeRecievedTime``` and ```nextAutomaticChannelSwitch``` seem to be set to sums of ```millis()``` added values in microseconds and then sometimes set to micros().  This seems inconsistent.

Are ```lastRadioPacketeRecievedTime``` and ```nextAutomaticChannelSwitch``` supposed to be in microseconds or milliseconds, or what?

(That said, just consistently using micros() doesn't yet help my packet success rate.)

soligen2010, 2021-11-10:
Well, it has been a very long time since I looked at this code, so I don't recall what I was thinking.  At a quick look at the code , using Micros seems to me to be appropriate, but I don't recall if there was something subtle making me use millis instead.  Probable warrants a deeper dive.

That said, I don't know if 100% reliability is a realistic goal in a dynamic environment - all the motion, varying antenna orientations, and very cheap radio modules.  Servos and electric motors make electrical noise.  The frequency space is shared with Wifi and other 2.4 GHz devices.  I only achieved it when testing at very short range.

Most RC control servos only update every 20 ms, and we send packets every 3 - 4 ms, so as long as every 5th packet gets through, you should never notice the difference.

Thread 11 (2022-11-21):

NO telemetry and servo no move in telemetry mode

pierrotm777, 2022-11-21:
Hello soligen,

I play with your receiver and your code.
For the transmitter i use a 4in1 module.
I can bind and unbind without problem.
If i use no telemetry mode, my servos are moving.
But if i use the Hub telemetry option, i have no telemetry and my servos don't move.

Any idea why please ?

Thanks for your help,

Pierre

stanekTM, 2022-11-21:
Hi Pierre,
you probably sent me an email that is intended for Soligen.

I sent you a video test of the OAVRC SPIRF and my RX FW, working both
without telemetry and with telemetry. I haven't tried OAVRC in SERIAL.
Probably a problem in the serial code.

video test cabell <https://photos.app.goo.gl/ZZWPxafreAFkarB98>

Best regards, Jiří

po 21. 11. 2022 v 19:24 odesílatel pierrotm777 ***@***.***>
napsal:

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

stanekTM, 2022-11-21:
Hi Pierre,

yes I'm using the latest sources, just my targets/mega2560... modified
"Mega 2560 PRO (Embed)" board pin mapping, TX CE pin to 3.3/5V.

Best regards, Jiří

po 21. 11. 2022 v 19:55 odesílatel pierrotm777 ***@***.***>
napsal:

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

soligen2010, 2022-11-23:
For 4 in one module, I suggest using my fork of multi protocol.  It is old,
but I have not tested new versions in a very long time, and I dont know if
something changed since my fork that may have broken something.

On another note.  Telemetry never really worked very well, so I don't use
it and would not recommend it.

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

pierrotm777, 2022-11-23:
Thanks soligen and Stanek 👍

stanekTM, 2022-11-23:
Hi Pierre,
You're welcome 🙂
So far I'm using everything on the ground, everything is ok there, I
haven't tested the CABELL telemetry on airplanes and longer distances, so I
can't confirm.

I fly my DIY RX Frsky D8 and DSM.

Another very interesting project is FHSS PHILL_G, there was a request to be
added to Multiprotocol, but without telemetry it is not very interesting
for me, it is vital for me to measure 1S lipo 😁, I love everything about
1S😍

I have some "Stanek" fixes to OAVRC_DEV... , but I'm probably the only
happy user, with a bunch of 1:32 buggy racers, so I'm not in a hurry.

Best regards, Jiří

st 23. 11. 2022 v 10:27 odesílatel pierrotm777 ***@***.***>
napsal:

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

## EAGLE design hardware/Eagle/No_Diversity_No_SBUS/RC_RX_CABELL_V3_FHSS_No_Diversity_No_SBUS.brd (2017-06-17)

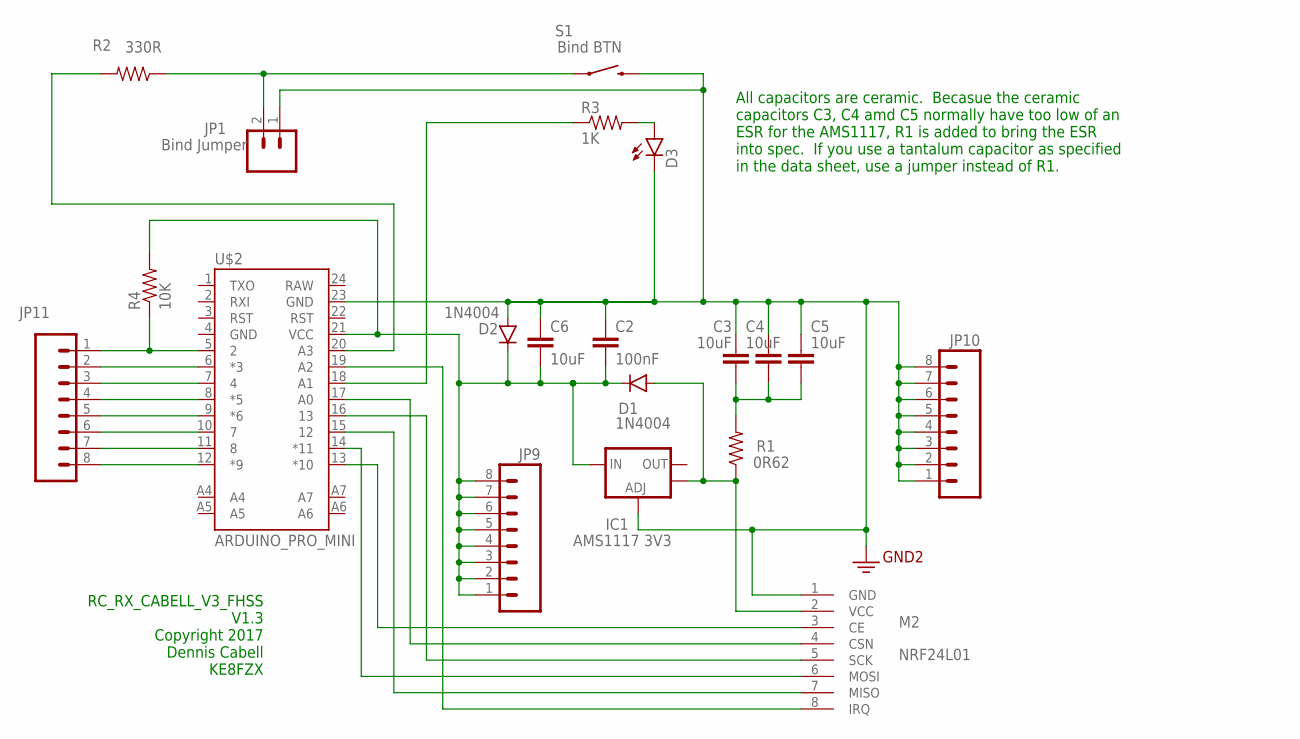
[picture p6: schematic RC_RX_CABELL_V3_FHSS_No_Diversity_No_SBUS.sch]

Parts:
C2: 100nF; CAP-PTH-5MM
C3, C4, C5, C6: 10uF; CAP-PTH-5MM
D1, D2: 1N4004; DIODE-1N4001
D3: LED3MM
IC1: AMS1117 3V3; SOT223
JP1: Bind Jumper; 1X02
JP9, JP10, JP11: M08; 1X08_ROUND
M2: NRF24L01; WIRELESS-NRF24L01
R1: 0R62; AXIAL-0.5
R2: 330R; AXIAL-0.3
R3: 1K; AXIAL-0.3
R4: 10K; AXIAL-0.3
S1: Bind BTN; TACTILE-SWITCH-1101NE
U$2: ARDUINO_PRO_MINI

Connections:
5V: C2.2, C6.2, D1.C, D2.C, IC1.3 (IN), JP9.1, JP9.2, JP9.3, JP9.4, JP9.5, JP9.6, JP9.7, JP9.8, R4.P$2 (2), U$2.21 (VCC)
GND: C2.1, C3.1, C4.1, C5.1, C6.1, D2.A, D3.K (C), IC1.1 (ADJ), JP1.1, JP10.1, JP10.2, JP10.3, JP10.4, JP10.5, JP10.6, JP10.7, JP10.8, M2.1 (GND), S1.2, U$2.23 (GND)
unnamed: JP11.1, R4.P$1 (1), U$2.5 (2)
unnamed: M2.3 (CE), U$2.13 (*10)
unnamed: JP11.2, U$2.6 (*3)
unnamed: JP11.3, U$2.7 (4)
unnamed: JP11.4, U$2.8 (*5)
unnamed: JP11.5, U$2.9 (*6)
unnamed: JP11.6, U$2.10 (7)
unnamed: JP11.7, U$2.11 (8)
unnamed: JP11.8, U$2.12 (*9)
unnamed: JP1.2, R2.P$1 (1), S1.1
unnamed: M2.8 (IRQ), U$2.19 (A2)
unnamed: C3.2, C4.2, C5.2, R1.P$2 (2)
unnamed: M2.5 (SCK), U$2.16 (13)
unnamed: M2.4 (CSN), U$2.17 (A0)
unnamed: D3.A, R3.P$2 (2)
unnamed: M2.6 (MOSI), U$2.14 (*11)
unnamed: R3.P$1 (1), U$2.18 (A1)
unnamed: M2.7 (MISO), U$2.15 (12)
unnamed: R2.P$2 (2), U$2.20 (A3)
VCC: D1.A, IC1.4 (OUT), M2.2 (VCC), R1.P$1 (1)

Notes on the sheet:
RC_RX_CABELL_V3_FHSS V1.3 Copyright 2017 Dennis Cabell KE8FZX
All capacitors are ceramic. Becasue the ceramic capacitors C3, C4 amd C5 normally have too low of an ESR for the AMS1117, R1 is added to bring the ESR into spec. If you use a tantalum capacitor as specified in the data sheet, use a jumper instead of R1.

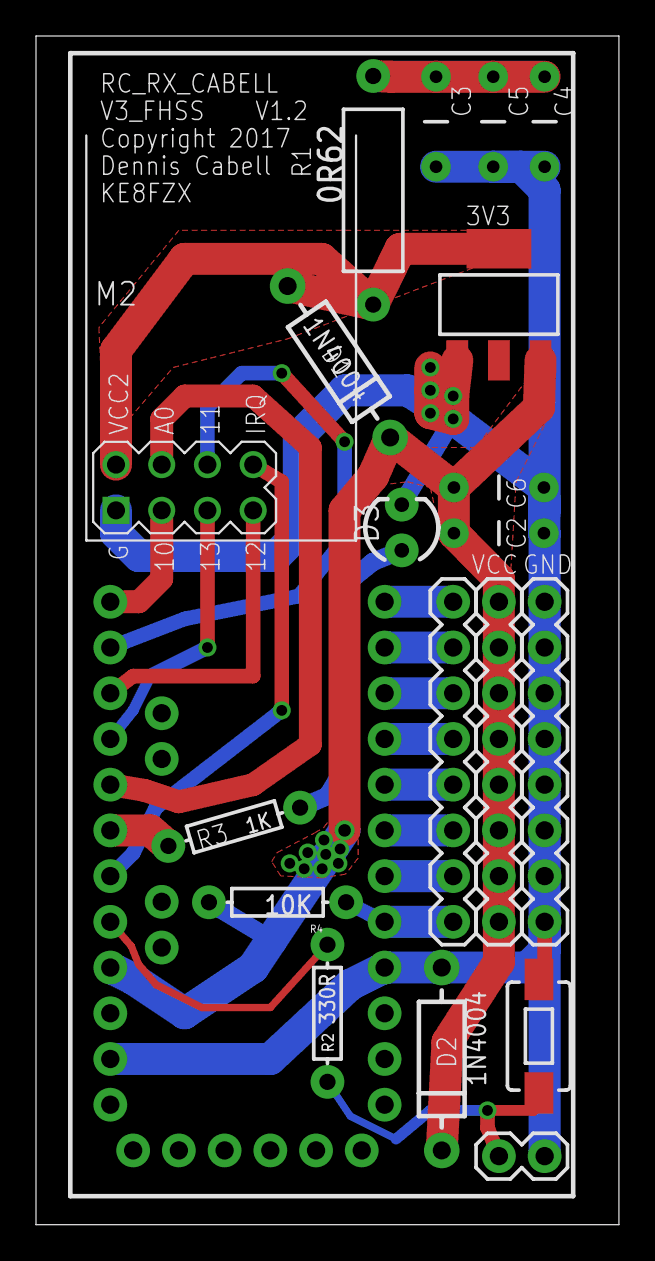
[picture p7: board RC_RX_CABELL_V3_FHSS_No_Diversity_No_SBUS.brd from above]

Board: 2 copper layers, 32.4 x 66.0 mm, 20 parts (0 on the bottom side), 22 nets.

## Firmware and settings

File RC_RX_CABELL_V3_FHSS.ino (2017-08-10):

/*
 Copyright 2017 by Dennis Cabell
 KE8FZX
 
 To use this software, you must adhere to the license terms described below, and assume all responsibility for the use
 of the software.  The user is responsible for all consequences or damage that may result from using this software.
 The user is responsible for ensuring that the hardware used to run this software complies with local regulations and that 
 any radio signal generated from use of this software is legal for that user to generate.  The author(s) of this software 
 assume no liability whatsoever.  The author(s) of this software is not responsible for legal or civil consequences of 
 using this software, including, but not limited to, any damages cause by lost control of a vehicle using this software.  
 If this software is copied or modified, this disclaimer must accompany all copies.
 
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
 You should have received a copy of the GNU General Public License
 along with RC_RX_CABELL_V3_FHSS.  If not, see <http://www.gnu.org/licenses/>.
 */
 
  /* Library dependencies:
   *  
   *  Aaduino Core, SPI, and EEPROM
   *    
   * https://github.com/nRF24/RF24 library copied and modified to streamline
   * opeerations specific to this application in order to improve loop timing.
   * See http://tmrh20.github.io/RF24  for documentation on the standard version of the library.
   *  
   * Arduino Servo was modified and is included with this source.  It was changed to not directly define the Timer 1 ISR
   */
   
#include "RX.h"
#include "Pins.h"

//--------------------------------------------------------------------------------------------------------------------------
void setup(void) {
  Serial.begin(74880);
  Serial.println(); Serial.println(F("Initializing"));
  
  pinMode (BIND_BUTTON_PIN,INPUT_PULLUP);  // used for bind plug or button

  pinMode (LED_PIN, OUTPUT);     //status LED
  digitalWrite(LED_PIN, LOW);

  ADC_Processing();   // Initial analog reads for A6/A7.  Initial call returns bad value so call 3 times to get a good starting value from each pin
  while (!bit_is_clear(ADCSRA, ADSC));  // wait for conversion
  ADC_Processing();
  while (!bit_is_clear(ADCSRA, ADSC));  // wait for conversion
  ADC_Processing();
 
  setupReciever();
  
  Serial.println(F("Starting main loop ")); 
}

//--------------------------------------------------------------------------------------------------------------------------
void loop() {  
  while (true) {               //loop forever without going back to Arduino core code
    if (getPacket()) {
      outputChannels();
    }
    ADC_Processing();   // Process ADC to asynchronously read A6 and A7 for telemetry analog values.  Non-blocking read
  }
}

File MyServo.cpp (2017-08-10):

//
// Copied from Arduino Servo library and changed to not use the interrupt 1 vector
// Instead in Interrupt 1 routine call MyServoInterruptOneProcessing().
// Also tweaked writeMicroseconds to only disable interrupts and change the ticks 
// value if the value has actually changed.
//

/*
 Servo.cpp - Interrupt driven Servo library for Arduino using 16 bit timers- Version 2
 Copyright (c) 2009 Michael Margolis.  All right reserved.

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
 You should have received a copy of the GNU Lesser General Public
 License along with this library; if not, write to the Free Software
 Foundation, Inc., 51 Franklin St, Fifth Floor, Boston, MA  02110-1301  USA
 */

#if defined(ARDUINO_ARCH_AVR)

#include <avr/interrupt.h>
#include <Arduino.h>

#include "MyServo.h"

#define usToTicks(_us)    (( clockCyclesPerMicrosecond()* _us) / 8)     // converts microseconds to tick (assumes prescale of 8)  // 12 Aug 2009
#define ticksToUs(_ticks) (( (unsigned)_ticks * 8)/ clockCyclesPerMicrosecond() ) // converts from ticks back to microseconds


#define TRIM_DURATION       2                               // compensation ticks to trim adjust for digitalWrite delays // 12 August 2009

//#define NBR_TIMERS        (MAX_SERVOS / SERVOS_PER_TIMER)

static servo_t servos[MAX_SERVOS];                          // static array of servo structures
static volatile int8_t Channel[_Nbr_16timers ];             // counter for the servo being pulsed for each timer (or -1 if refresh interval)

uint8_t ServoCount = 0;                                     // the total number of attached servos


// convenience macros
#define SERVO_INDEX_TO_TIMER(_servo_nbr) ((timer16_Sequence_t)(_servo_nbr / SERVOS_PER_TIMER)) // returns the timer controlling this servo
#define SERVO_INDEX_TO_CHANNEL(_servo_nbr) (_servo_nbr % SERVOS_PER_TIMER)       // returns the index of the servo on this timer
#define SERVO_INDEX(_timer,_channel)  ((_timer*SERVOS_PER_TIMER) + _channel)     // macro to access servo index by timer and channel
#define SERVO(_timer,_channel)  (servos[SERVO_INDEX(_timer,_channel)])            // macro to access servo class by timer and channel

#define SERVO_MIN() (MIN_PULSE_WIDTH - this->min * 4)  // minimum value in uS for this servo
#define SERVO_MAX() (MAX_PULSE_WIDTH - this->max * 4)  // maximum value in uS for this servo

/************ static functions common to all instances ***********************/

static inline void handle_interrupts(timer16_Sequence_t timer, volatile uint16_t *TCNTn, volatile uint16_t* OCRnA)
{
  if( Channel[timer] < 0 )
    *TCNTn = 0; // channel set to -1 indicated that refresh interval completed so reset the timer
  else{
    if( SERVO_INDEX(timer,Channel[timer]) < ServoCount && SERVO(timer,Channel[timer]).Pin.isActive == true )
      digitalWrite( SERVO(timer,Channel[timer]).Pin.nbr,LOW); // pulse this channel low if activated
  }

  Channel[timer]++;    // increment to the next channel
  if( SERVO_INDEX(timer,Channel[timer]) < ServoCount && Channel[timer] < SERVOS_PER_TIMER) {
    *OCRnA = *TCNTn + SERVO(timer,Channel[timer]).ticks;
    if(SERVO(timer,Channel[timer]).Pin.isActive == true)     // check if activated
      digitalWrite( SERVO(timer,Channel[timer]).Pin.nbr,HIGH); // its an active channel so pulse it high
  }
  else {
    // finished all channels so wait for the refresh period to expire before starting over
    if( ((unsigned)*TCNTn) + 4 < usToTicks(REFRESH_INTERVAL) )  // allow a few ticks to ensure the next OCR1A not missed
      *OCRnA = (unsigned int)usToTicks(REFRESH_INTERVAL);
    else
      *OCRnA = *TCNTn + 4;  // at least REFRESH_INTERVAL has elapsed
    Channel[timer] = -1; // this will get incremented at the end of the refresh period to start again at the first channel
  }
}

#ifndef WIRING // Wiring pre-defines signal handlers so don't define any if compiling for the Wiring platform
// Interrupt handlers for Arduino
#if defined(_useTimer1)
void MyServoInterruptOneProcessing()
{
  handle_interrupts(_timer1, &TCNT1, &OCR1A);
}
#endif

#if defined(_useTimer3)
SIGNAL (TIMER3_COMPA_vect)
{
  handle_interrupts(_timer3, &TCNT3, &OCR3A);
}
#endif

#if defined(_useTimer4)
SIGNAL (TIMER4_COMPA_vect)
{
  handle_interrupts(_timer4, &TCNT4, &OCR4A);
}
#endif

#if defined(_useTimer5)
SIGNAL (TIMER5_COMPA_vect)
{
  handle_interrupts(_timer5, &TCNT5, &OCR5A);
}
#endif

#elif defined WIRING
// Interrupt handlers for Wiring
#if defined(_useTimer1)
void Timer1Service()
{
  handle_interrupts(_timer1, &TCNT1, &OCR1A);
}
#endif
#if defined(_useTimer3)
void Timer3Service()
{
  handle_interrupts(_timer3, &TCNT3, &OCR3A);
}
#endif
#endif


static void initISR(timer16_Sequence_t timer)
{
#if defined (_useTimer1)
  if(timer == _timer1) {
    TCCR1A = 0;             // normal counting mode
    TCCR1B = _BV(CS11);     // set prescaler of 8
    TCNT1 = 0;              // clear the timer count
#if defined(__AVR_ATmega8__)|| defined(__AVR_ATmega128__)
    TIFR |= _BV(OCF1A);      // clear any pending interrupts;
    TIMSK |=  _BV(OCIE1A) ;  // enable the output compare interrupt
#else
    // here if not ATmega8 or ATmega128
    TIFR1 |= _BV(OCF1A);     // clear any pending interrupts;
    TIMSK1 |=  _BV(OCIE1A) ; // enable the output compare interrupt
#endif
#if defined(WIRING)
    timerAttach(TIMER1OUTCOMPAREA_INT, Timer1Service);
#endif
  }
#endif

#if defined (_useTimer3)
  if(timer == _timer3) {
    TCCR3A = 0;             // normal counting mode
    TCCR3B = _BV(CS31);     // set prescaler of 8
    TCNT3 = 0;              // clear the timer count
#if defined(__AVR_ATmega128__)
    TIFR |= _BV(OCF3A);     // clear any pending interrupts;
  ETIMSK |= _BV(OCIE3A);  // enable the output compare interrupt
#else
    TIFR3 = _BV(OCF3A);     // clear any pending interrupts;
    TIMSK3 =  _BV(OCIE3A) ; // enable the output compare interrupt
#endif
#if defined(WIRING)
    timerAttach(TIMER3OUTCOMPAREA_INT, Timer3Service);  // for Wiring platform only
#endif
  }
#endif

#if defined (_useTimer4)
  if(timer == _timer4) {
    TCCR4A = 0;             // normal counting mode
    TCCR4B = _BV(CS41);     // set prescaler of 8
    TCNT4 = 0;              // clear the timer count
    TIFR4 = _BV(OCF4A);     // clear any pending interrupts;
    TIMSK4 =  _BV(OCIE4A) ; // enable the output compare interrupt
  }
#endif

#if defined (_useTimer5)
  if(timer == _timer5) {
    TCCR5A = 0;             // normal counting mode
    TCCR5B = _BV(CS51);     // set prescaler of 8
    TCNT5 = 0;              // clear the timer count
    TIFR5 = _BV(OCF5A);     // clear any pending interrupts;
    TIMSK5 =  _BV(OCIE5A) ; // enable the output compare interrupt
  }
#endif
}
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

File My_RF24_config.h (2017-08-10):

//
// Copied from https://github.com/nRF24/RF24 library and changed to streamline
// operations specific to this application
//
/*
 Copyright (C) 2011 J. Coliz <maniacbug@ymail.com>

 This program is free software; you can redistribute it and/or
 modify it under the terms of the GNU General Public License
 version 2 as published by the Free Software Foundation.
 */
 
 /* spaniakos <spaniakos@gmail.com>
  Added __ARDUINO_X86__ support
*/

#ifndef __RF24_CONFIG_H__
#define __RF24_CONFIG_H__

  /*** USER DEFINES:  ***/  
  //#define FAILURE_HANDLING
  //#define SERIAL_DEBUG
  #define MINIMAL
  //#define SPI_UART  // Requires library from https://github.com/TMRh20/Sketches/tree/master/SPI_UART
  //#define SOFTSPI   // Requires library from https://github.com/greiman/DigitalIO
  
  /**********************/
  #define rf24_max(a,b) (a>b?a:b)
  #define rf24_min(a,b) (a<b?a:b)

  #if defined SPI_HAS_TRANSACTION && !defined SPI_UART && !defined SOFTSPI
    #define RF24_SPI_TRANSACTIONS
  #endif
 
 
//ATXMega
#if defined(__AVR_ATxmega64D3__) || defined(__AVR_ATxmega128D3__) || defined(__AVR_ATxmega192D3__) || defined(__AVR_ATxmega256D3__) || defined(__AVR_ATxmega384D3__) // In order to be available both in windows and linux this should take presence here.
  #define XMEGA
  #define XMEGA_D3
  #include "utility/ATXMegaD3/RF24_arch_config.h"
#elif ( !defined (ARDUINO) ) // Any non-arduino device is handled via configure/Makefile

  // The configure script detects device and copies the correct includes.h file to /utility/includes.h
  // This behavior can be overridden by calling configure with respective parameters
  // The includes.h file defines either RF24_RPi, MRAA, LITTLEWIRE or RF24_SPIDEV and includes the correct RF24_arch_config.h file
  #include "utility/includes.h"

//ATTiny  
#elif defined(__AVR_ATtiny25__) || defined(__AVR_ATtiny45__) || defined(__AVR_ATtiny85__) || defined(__AVR_ATtiny24__) || defined(__AVR_ATtiny44__) || defined(__AVR_ATtiny84__) || defined(__AVR_ATtiny2313__) || defined(__AVR_ATtiny4313__) || defined(__AVR_ATtiny861__)  
  #define RF24_TINY
  #include "utility/ATTiny/RF24_arch_config.h"


//LittleWire  
#elif defined(LITTLEWIRE)
  
  #include "utility/LittleWire/RF24_arch_config.h"

//Teensy  
#elif defined (TEENSYDUINO)

  #include "utility/Teensy/RF24_arch_config.h"  
//Everything else
#else 

  #include <Arduino.h>
  
  // RF modules support 10 Mhz SPI bus speed
  const uint32_t RF24_SPI_SPEED = 10000000;  

#if defined (ARDUINO) && !defined (__arm__) && !defined (__ARDUINO_X86__)
      #if defined SPI_UART
		#include <SPI_UART.h>
		#define _SPI uspi
	  #elif defined SOFTSPI
	  // change these pins to your liking
      //
      const uint8_t SOFT_SPI_MISO_PIN = 16; 
      const uint8_t SOFT_SPI_MOSI_PIN = 15; 
      const uint8_t SOFT_SPI_SCK_PIN = 14;  
      const uint8_t SPI_MODE = 0;
      #define _SPI spi
      
	  #else	    
		#include <SPI.h>
		#define _SPI SPI
	  #endif
#else
  // Define _BV for non-Arduino platforms and for Arduino DUE
  #include <stdint.h>
  #include <stdio.h>
  #include <string.h>


 #if defined(__arm__) || defined (__ARDUINO_X86__)
   #if defined (__arm__) && defined (SPI_UART)
		#include <SPI_UART.h>
		#define _SPI uspi
   #else
     #include <SPI.h>
     #define _SPI SPI
   #endif
 #elif !defined(__arm__) && !defined (__ARDUINO_X86__)
   extern HardwareSPI SPI;
 #endif
 
 #define _BV(x) (1<<(x))
  
#endif

  #ifdef SERIAL_DEBUG
	#define IF_SERIAL_DEBUG(x) ({x;})
  #else
	#define IF_SERIAL_DEBUG(x)
	#if defined(RF24_TINY)
	#define printf_P(...)
    #endif
  #endif
  
#if  defined (__ARDUINO_X86__)
	#define printf_P printf
	#define _BV(bit) (1<<(bit))
#endif
  
// Progmem is Arduino-specific
// Arduino DUE is arm and does not include avr/pgmspace
#if defined (ARDUINO_ARCH_ESP8266)

  #define PSTR(x) (x)
  #define printf Serial.printf
  #define sprintf(...) os_sprintf( __VA_ARGS__ )
  #define printf_P printf
  #define strlen_P strlen  
  #define PROGMEM
  #define pgm_read_byte(addr) (*(const unsigned char *)(addr))
  #define pgm_read_word(p) (*(p))
  #define PRIPSTR "%s"

#elif defined(ARDUINO) && ! defined(__arm__) && !defined (__ARDUINO_X86__) || defined(XMEGA)
	#include <avr/pgmspace.h>
	#define PRIPSTR "%S"
#else
  #if ! defined(ARDUINO) // This doesn't work on Arduino DUE
	typedef char const char;
  #else // Fill in pgm_read_byte that is used, but missing from DUE
	#define pgm_read_byte(addr) (*(const unsigned char *)(addr))
  #endif


  typedef uint16_t prog_uint16_t;
  #define PSTR(x) (x)
  #define printf_P printf
  #define strlen_P strlen
  #define PROGMEM
  #define pgm_read_word(p) (*(p))

  #define PRIPSTR "%s"

#endif

#endif



#endif // __RF24_CONFIG_H__

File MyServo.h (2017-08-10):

//
// Changed to not use the interrupt 1 vector
// in your own Interrupt 1 routing call interruptOneProcessing()
//

/*
  Servo.h - Interrupt driven Servo library for Arduino using 16 bit timers- Version 2
  Copyright (c) 2009 Michael Margolis.  All right reserved.

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
  You should have received a copy of the GNU Lesser General Public
  License along with this library; if not, write to the Free Software
  Foundation, Inc., 51 Franklin St, Fifth Floor, Boston, MA  02110-1301  USA
*/

/* 
  A servo is activated by creating an instance of the Servo class passing 
  the desired pin to the attach() method.
  The servos are pulsed in the background using the value most recently 
  written using the write() method.

  Note that analogWrite of PWM on pins associated with the timer are 
  disabled when the first servo is attached.
  Timers are seized as needed in groups of 12 servos - 24 servos use two 
  timers, 48 servos will use four.
  The sequence used to sieze timers is defined in timers.h

  The methods are:

    Servo - Class for manipulating servo motors connected to Arduino pins.

    attach(pin )  - Attaches a servo motor to an i/o pin.
    attach(pin, min, max  ) - Attaches to a pin setting min and max values in microseconds
    default min is 544, max is 2400  
 
    write()     - Sets the servo angle in degrees.  (invalid angle that is valid as pulse in microseconds is treated as microseconds)
    writeMicroseconds() - Sets the servo pulse width in microseconds 
    read()      - Gets the last written servo pulse width as an angle between 0 and 180. 
    readMicroseconds()   - Gets the last written servo pulse width in microseconds. (was read_us() in first release)
    attached()  - Returns true if there is a servo attached. 
    detach()    - Stops an attached servos from pulsing its i/o pin. 
 */

#ifndef Servo_h
#define Servo_h

#include <inttypes.h>

/* 
 * Defines for 16 bit timers used with  Servo library 
 *
 * If _useTimerX is defined then TimerX is a 16 bit timer on the current board
 * timer16_Sequence_t enumerates the sequence that the timers should be allocated
 * _Nbr_16timers indicates how many 16 bit timers are available.
 */

// Architecture specific include
#if defined(ARDUINO_ARCH_AVR)
/**
 * AVR Only definitions
 * --------------------
 */

// Say which 16 bit timers can be used and in what order
#if defined(__AVR_ATmega1280__) || defined(__AVR_ATmega2560__)
#define _useTimer5
#define _useTimer1
#define _useTimer3
#define _useTimer4
typedef enum { _timer5, _timer1, _timer3, _timer4, _Nbr_16timers } timer16_Sequence_t;

#elif defined(__AVR_ATmega32U4__)
#define _useTimer1
typedef enum { _timer1, _Nbr_16timers } timer16_Sequence_t;

#elif defined(__AVR_AT90USB646__) || defined(__AVR_AT90USB1286__)
#define _useTimer3
#define _useTimer1
typedef enum { _timer3, _timer1, _Nbr_16timers } timer16_Sequence_t;

#elif defined(__AVR_ATmega128__) || defined(__AVR_ATmega1281__) || defined(__AVR_ATmega1284__) || defined(__AVR_ATmega1284P__) || defined(__AVR_ATmega2561__)
#define _useTimer3
#define _useTimer1
typedef enum { _timer3, _timer1, _Nbr_16timers } timer16_Sequence_t;

#else  // everything else
#define _useTimer1
typedef enum { _timer1, _Nbr_16timers } timer16_Sequence_t;
#endif
#else
#error "This library only supports boards with an AVR processor."
#endif

#define Servo_VERSION           2     // software version of this library

#define MIN_PULSE_WIDTH       544     // the shortest pulse sent to a servo  
#define MAX_PULSE_WIDTH      2400     // the longest pulse sent to a servo 
#define DEFAULT_PULSE_WIDTH  1500     // default pulse width when servo is attached
#define REFRESH_INTERVAL    20000     // minumim time to refresh servos in microseconds 

#define SERVOS_PER_TIMER       12     // the maximum number of servos controlled by one timer 
#define MAX_SERVOS   (_Nbr_16timers  * SERVOS_PER_TIMER)

#define INVALID_SERVO         255     // flag indicating an invalid servo index

typedef struct  {
  uint8_t nbr        :6 ;             // a pin number from 0 to 63
  uint8_t isActive   :1 ;             // true if this channel is enabled, pin not pulsed if false 
} ServoPin_t   ;  

typedef struct {
  ServoPin_t Pin;
  volatile unsigned int ticks;
} servo_t;

void MyServoInterruptOneProcessing();

class MyServo
{
public:
  MyServo();
  uint8_t attach(int pin);           // attach the given pin to the next free channel, sets pinMode, returns channel number or 0 if failure
  uint8_t attach(int pin, int min, int max); // as above but also sets min and max values for writes. 
  void detach();
  void write(int value);             // if value is < 200 its treated as an angle, otherwise as pulse width in microseconds 
  void writeMicroseconds(unsigned int value); // Write pulse width in microseconds 
  int read();                        // returns current pulse width as an angle between 0 and 180 degrees
  int readMicroseconds();            // returns current pulse width in microseconds for this servo (was read_us() in first release)
  bool attached();                   // return true if this servo is attached, otherwise false 
private:
   uint8_t servoIndex;               // index into the channel data for this servo
   int8_t min;                       // minimum is this value times 4 added to MIN_PULSE_WIDTH    
   int8_t max;                       // maximum is this value times 4 added to MAX_PULSE_WIDTH   
};

#endif

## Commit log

2017-03-15 Fixed bug in processing unBind command from TX
    [RX.cpp]
2017-04-11 Changed Bind pin to A3, Added Eagle files
    This frees A4 for potential use of I2C bus in the future
    [RC_RX_CABELL_V3_FHSS.brd, RC_RX_CABELL_V3_FHSS.sch]
2017-04-13 Fixed compile issue in arduino 1.6.8
    [MyServo.cpp]
2017-04-13 comments about encoder library
2017-04-16 SUM_PPM constrain max PPM channels to 8 to ensure fits frame size
2017-04-19 Analog telemetry from A6/A7, Telemetry packet Xmits sooner, Checksum field split to avoid endian issue
    [Pins.h, RX.cpp, RX.h]
2017-04-25 Removed non-IRQ operation in favcor of IRQs
    REmoved entirely polling the NRF24l01 as polling during RX or TX might
    cause reliability issue.
    [Pins.h, RX.cpp, RX.h]
2017-05-02 Read analog pins asynchonously with interrupt
2017-05-02 Moved RxMOde bit flip to proper place
    [RX.cpp]
2017-05-02 Re-arm thottle if within 10 of min value (within 1%)
2017-05-02 typos fixed in comments
    [RX.cpp]
2017-05-02 Completion of async adc code
2017-05-12 Reduced servo jitter
    Turned off timer0 ISR and replaced with time functions that dont use
    ISRs
    [RC_RX_CABELL_V3_FHSS.ino, RX.cpp, RX.h]
2017-05-12 Disarm throttle one second after startup if no signal recieved
2017-05-12 Honor the MAx Power Override bit in the option byte when sending telemetry packets
2017-05-14 Removed myMicros - going back to arduino micros()
    myMicros turned out to be unreliable. Using micros() is much more
    reliable. We will just have to tolerate the little bit of servo jitter
    this may cause.
    [MyServo.cpp, RC_RX_CABELL_V3_FHSS.ino, RX.h]
2017-05-14 Removed myMicros - going back to arduino micros()
2017-05-18 Schematic with Diversity
    [RC_RX_CABELL_V3_FHSS_No_Diversity.brd, RC_RX_CABELL_V3_FHSS_No_Diversity.sch, RC_RX_CABELL_V3_FHSS_With_Diversity.sch]
2017-06-01 Change MyServo.writeMicroseconds to only disable interrupts and change the ticks if teh value actually changed
    channels 4 to 8 rarely change packet to packet, so this reduces time
    spent with interrupts disabled
2017-06-01 Disable interrupts when updating SUM PPM values, but not of the value hasnt changed
2017-06-02 Calibrated and PPM and optimized the PPM ISR
2017-06-04 Avoid Serial.print when on SBUS mode becasue SBUS used UART
    [RX.cpp, RX.h]
2017-06-11 Added option for I2C LCD for Test Harness
2017-06-13 Corrected packet timing when secondary reciever used
    [RX.cpp]
2017-06-17 Hardware Updates for SBUS & PPM
    [RC_RX_CABELL_V3_FHSS_No_Diversity_No_SBUS.brd, RC_RX_CABELL_V3_FHSS_No_Diversity_No_SBUS.sch, RC_RX_CABELL_V3_FHSS_With_Diversity_With_SBUS.brd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]
2017-06-18 Fully reset test harness display after failsafe/resync
    [TestHarness.cpp]
2017-06-24 Calibrated PPM using betaflight on F4 board
2017-08-10 Fix typos in comments
    [MyServo.cpp, MyServo.h, My_RF24.cpp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]
2017-08-10 Comment Typos; More stringent signal lock on power on.
    First time syncing teh hopping when powered on be more stringent. Must
    have stong signal on all 45 channels to lock in signal for first time.
    After initial lock use the previous less stringent method. This is to
    help ensure a strong lock on power up when initially connecting model to
    transmitter.
2017-08-10 Wait for conversions to finish on initializing ADC calls
2017-10-14 Testharness doesn't repeatedly display Re-sync
    In some cases when Re-syncing while in test harness mode the LCD was
    constantly being refreshed. This change displays the Re-sync message
    only once.
    [TestHarness.cpp]
2019-01-21 Fixed case of includes
    needed for compiling on Linux
    [SUM_PPM.h]
2019-01-21 Get current channel from reserved byte
    At close range the packet can be recieved on an adjacent channel. This sets the current channel to the channel teh TX sent the packet on so the correct next channel is calculated.
    [RX.cpp]
2019-01-21 Get Current Channel from Reserved Byte
    and formatting changes
2019-01-21 CurrentChannel Fix
2019-01-21 Added No Pulses Failsafe
    Experimental
    [RX.cpp, RX.h]
2019-01-23 Seperate #define for CE pins set = csn pin
2019-01-23 EAsier to set custom throttle value for disarmed state
    THROTTLE_DISARM_VALUE added to RX.h
2019-01-24 Update TestHarness.h
    fix anoying special character at end of file
    [TestHarness.h]

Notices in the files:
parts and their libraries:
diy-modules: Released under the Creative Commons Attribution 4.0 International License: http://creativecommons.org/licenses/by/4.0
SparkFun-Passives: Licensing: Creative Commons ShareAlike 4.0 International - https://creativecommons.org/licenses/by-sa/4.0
